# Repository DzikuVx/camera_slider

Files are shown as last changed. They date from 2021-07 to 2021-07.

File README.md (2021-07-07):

# DIY Motorized Camera Slider

Video presentation https://youtu.be/z8LCp77dOxo

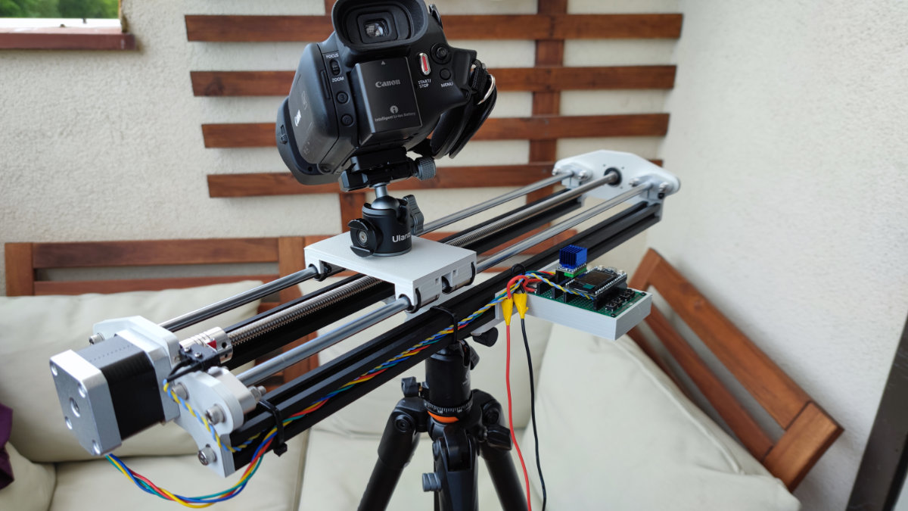
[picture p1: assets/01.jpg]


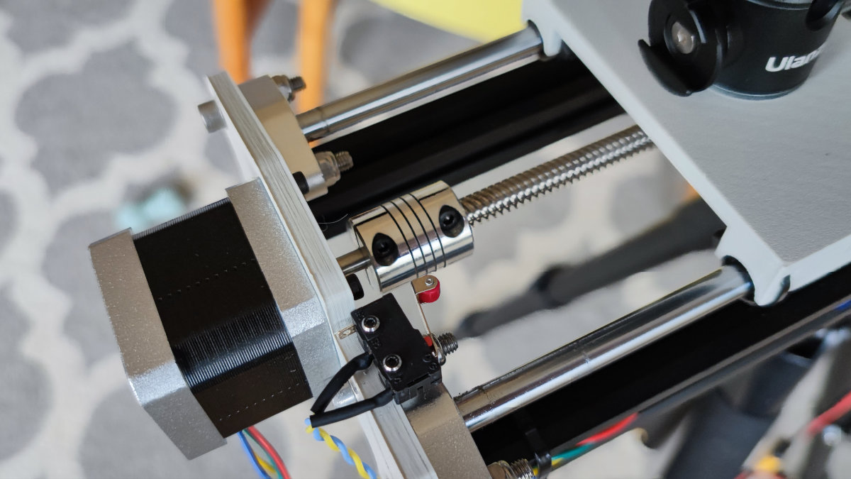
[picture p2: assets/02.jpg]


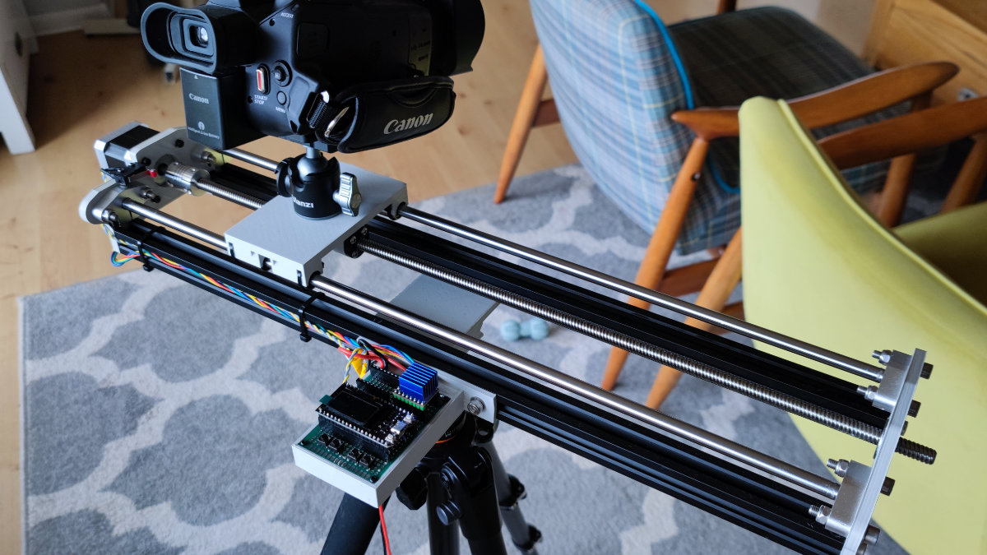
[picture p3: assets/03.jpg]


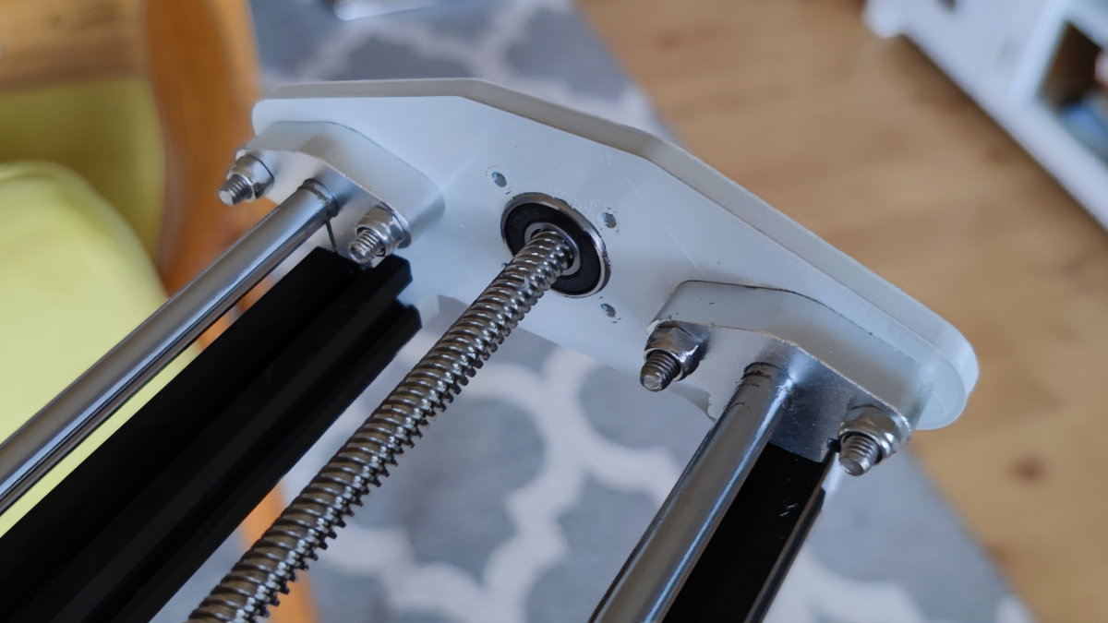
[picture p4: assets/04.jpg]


# ESP32 pinouts

| Function | ESP32 pin |
| --- | --- |
| TMC2209 direction pin | 13 |
| TMC2209 step pin | 12 |
| End-stop switch | 17 |
| TMC2209 Enable | 14 |
| Button #1 | 21 |
| Button #1 | 22 |
| Button #1 | 19 |
| Button #1 | 23 |

# User interface

Web Interface over WiFi is recommended. Connect to `DiyCameraSlider` WiFi with password `123456789` and use `http://192.168.4.1` URL.

Buttons are for emergency situations.

# Other

* TMC2209 should be configured in 8 microstep mode - MS1 and MS2 pulled to GND
* Tripod mount is compatible with Arca Swiss

#  Dependencies

* [AsyncTCP](https://github.com/me-no-dev/AsyncTCP)
* [ESPAsyncWebServer](https://github.com/me-no-dev/ESPAsyncWebServer)

# BOM

* [TTGO ESP32 with OLED](https://bit.ly/2G3qTSO)
* [TMC2209 stepper driver](https://bit.ly/3yxFSKa)
* [Tactile buttons](http://bit.ly/2Kzawy3)
* 60x90 universal PCB
* [TR8 8mm lead screw nut](https://bit.ly/3jS5PQQ)
* [NEMA17 stepper motor](https://bit.ly/3yv4bZh)
* [T8 8mm lead screw](https://bit.ly/3hDNhRs)
* [2x 500mm linear rod 8mm diameter](https://bit.ly/3eajnDF)
* [5x8mm coupler](https://bit.ly/3dMOrZR)
* [4x linear rod holder](https://bit.ly/3xndEBR)
* [4x LM8UU linear bearings](https://bit.ly/36hJqUK)
* 608 2RS 8x22x7mm bearing
* [Tripod head](https://bit.ly/3wtL7te)
* Tripod screw to attach the head
* 2x 500mm  2020 V-slot alu profiles
* 2020 hammer nuts
* M3 and M5 nuts and screws
* End switch
* 5V stepdown voltage regulator
* cables

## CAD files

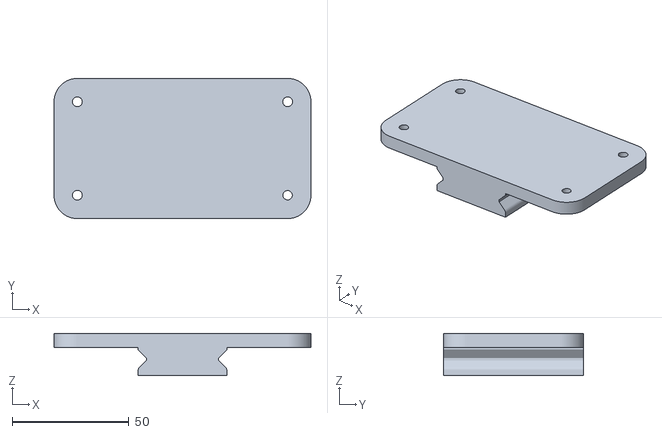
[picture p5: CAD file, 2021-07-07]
stl/tripod-mount.stl
110.0 x 60.0 x 18.0

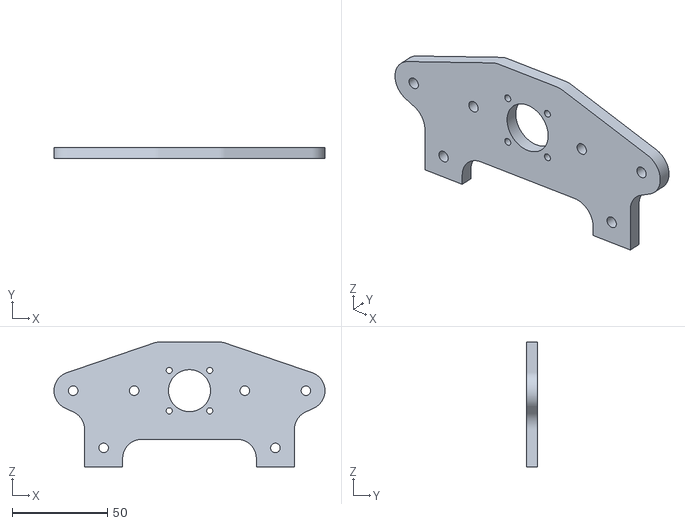
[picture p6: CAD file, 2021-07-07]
stl/end-plate-b.stl
142.0 x 6.00 x 65.5

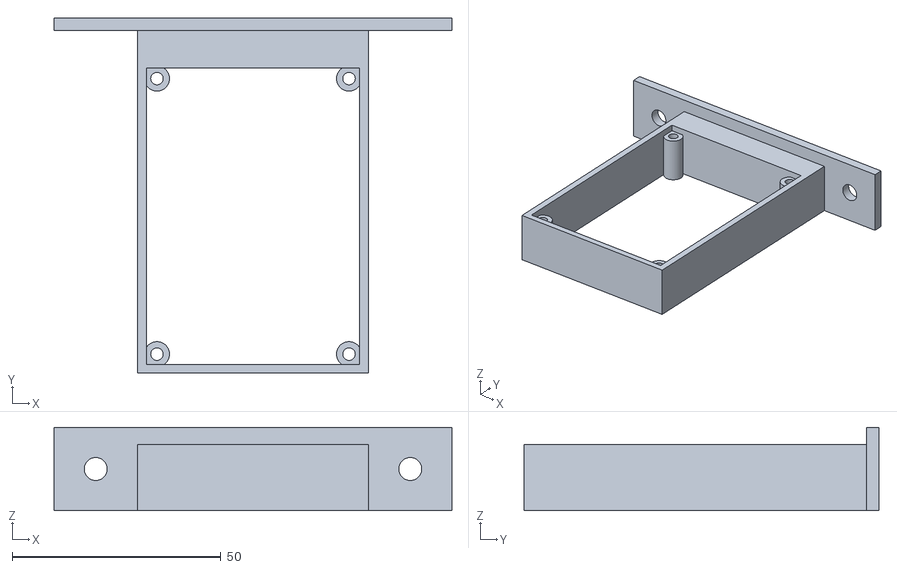
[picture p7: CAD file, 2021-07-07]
stl/pcb-holder.stl
95.3 x 85.0 x 20.0

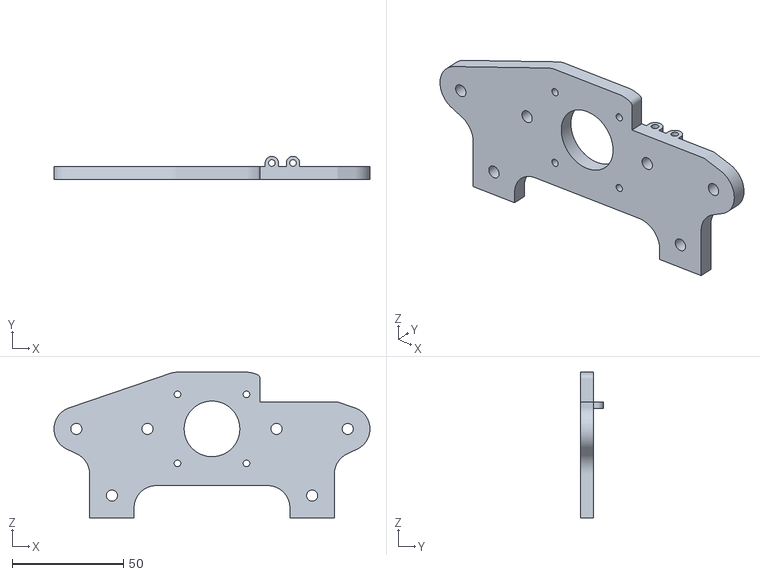
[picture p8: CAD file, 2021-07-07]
stl/end-plate-a.stl
142.0 x 10.5 x 65.5

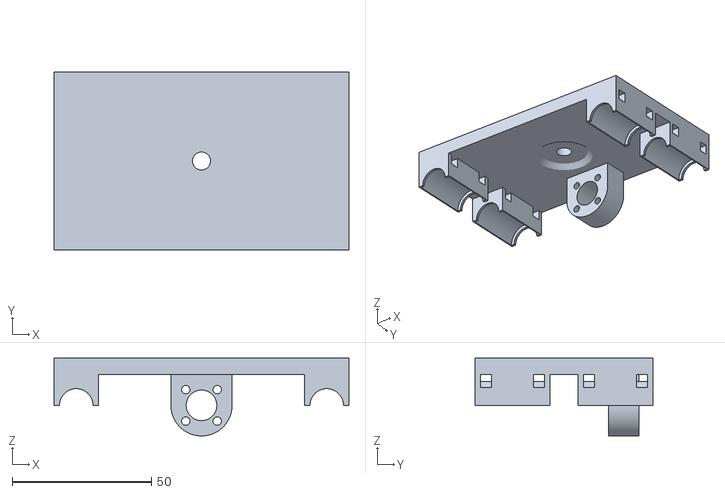
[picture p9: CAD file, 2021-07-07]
stl/platform.stl
106.0 x 64.0 x 28.0

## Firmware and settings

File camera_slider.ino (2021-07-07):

// #include <Wire.h>
#include "QmuTactile.h"
#include "filter.h"
#include <WiFi.h>
#include <AsyncTCP.h>
#include <ESPAsyncWebServer.h>

#define PID_UPDATE_TASK_MS 50

#define PIN_STEP1_DIRECTION 13
#define PIN_STEP1_STEP 12

#define PIN_STEP2_DIRECTION 18
#define PIN_STEP2_STEP 5

#define PIN_END_STOP 17

#define PIN_STEP_ENABLE 14

#define PIN_BUTTON_1 21
#define PIN_BUTTON_2 22
#define PIN_BUTTON_3 19
#define PIN_BUTTON_4 23

#define I2C1_SDA_PIN 4
#define I2C1_SCL_PIN 15

#define I2C2_SDA_PIN 27
#define I2C2_SCL_PIN 26

// TwoWire I2C1 = TwoWire(0); //OLED bus
// TwoWire I2C2 = TwoWire(1); //VL53L0X bus

QmuTactile button1(PIN_BUTTON_1);
QmuTactile button2(PIN_BUTTON_2);
QmuTactile button3(PIN_BUTTON_3);
QmuTactile button4(PIN_BUTTON_4);
QmuTactile buttonEnd(PIN_END_STOP);

// TaskHandle_t driverPid;


// QmuPid distanceToStep(0.1, 0, 50, 0);

// Adafruit_VL53L0X lox = Adafruit_VL53L0X();

enum systemFlags_e
{
  SYSTEM_FLAG_NONE = 0,                  //  0
  SYSTEM_FLAG_NEEDS_CALIBRATION = 1 << 0,  //  1
  SYSTEM_FLAG_CALIBRATING = 1 << 1,     //  2
  SYSTEM_FLAG_OPERATIONAL = 1 << 2, // 4 
  SYSTEM_FLAG_FORCE_FORWARD = 1 << 3, // 8 
  SYSTEM_FLAG_MOVE_TO_POSITION = 1 << 4, // 8 
  SYSTEM_FLAG_EMERGENCY_STOP = 1 << 5, // 8 
  SYSTEM_FLAG_REQUESTING_POSITION = 1 << 6, // 16
};

uint8_t _systemFlags;
pt1Filter_t targetPositionFilter;

volatile int stepsPerSecond[2] = {0};

#define SPEED_SLOW 750
#define SPEED_MID 1500
#define SPEED_FAST 3000

int32_t maxSpeed = SPEED_MID;

int32_t currentPosition[2] = {0};   
int32_t targetPosition[2] = {0};    //Hardware operated Position
int32_t requestedPosition[2] = {0}; //User requested Position

AsyncWebServer server(80);

const char* ssid = "DiyCameraSlider";
const char* password = "123456789";

void notFound(AsyncWebServerRequest *request) {
    request->send(404, "text/plain", "Not found");
}

String pageContent() {
    String pageContent;
    pageContent = "<!DOCTYPE html><html>";
    pageContent += "<head><meta name=\"viewport\" content=\"width=device-width, initial-scale=1\">";
    pageContent += "<link rel=\"icon\" href=\"data:,\">";
    pageContent += "<style>html { font-family: Helvetica; display: inline-block; margin: 0px auto; text-align: center;}";
    pageContent += ".button { background-color: #4CAF50; border: none; color: white; padding: 16px 40px; text-decoration: none; font-size: 30px; margin: 2px; cursor: pointer;}";
    pageContent += ".button-small { background-color: #0000ff; border: none; color: white; padding: 8px 20px; text-decoration: none; font-size: 15px; margin: 2px; cursor: pointer;}";
    pageContent += ".button2 {background-color: #ff0000;}</style></head>";
    
    pageContent += "<body><h1>DIY Camera Slider</h1>";
    
    pageContent += "<p><a href=\"/forward\"><button class=\"button\">Forward</button></a></p>";
    pageContent += "<p><a href=\"/stop\"><button class=\"button button2\">Stop</button></a></p>";
    pageContent += "<p><a href=\"/backward\"><button class=\"button\">Backward</button></a></p>";
    
    pageContent += "<p>";
    pageContent += "<a href=\"/slow\"><button class=\"button-small\">Slow</button></a>";
    pageContent += "<a href=\"/mid\"><button class=\"button-small\">Mid</button></a>";
    pageContent += "<a href=\"/fast\"><button class=\"button-small\">Fast</button></a>";
    pageContent += "</p>";

    pageContent += "</body></html>";

    return pageContent;
}

void setup()
{
    Serial.begin(115200);

    WiFi.softAP(ssid, password);
    IPAddress IP = WiFi.softAPIP();
    Serial.print("AP IP address: ");
    Serial.println(IP);

    server.on("/", HTTP_GET, [](AsyncWebServerRequest *request){
        request->send(200, "text/html", pageContent());
    });

    server.on("/forward", HTTP_GET, [](AsyncWebServerRequest *request){
        requestedPosition[0] = 81000;
        _systemFlags |= SYSTEM_FLAG_REQUESTING_POSITION;
        request->send(200, "text/html", pageContent());
    });

    server.on("/backward", HTTP_GET, [](AsyncWebServerRequest *request){
        requestedPosition[0] = 0;
        _systemFlags |= SYSTEM_FLAG_REQUESTING_POSITION;
        request->send(200, "text/html", pageContent());
    });

    server.on("/stop", HTTP_GET, [](AsyncWebServerRequest *request){
        requestedPosition[0] = currentPosition[0];
        targetPosition[0] = currentPosition[0];
        _systemFlags |= SYSTEM_FLAG_REQUESTING_POSITION;
        request->send(200, "text/html", pageContent());
    });

    server.on("/slow", HTTP_GET, [](AsyncWebServerRequest *request){
        maxSpeed = SPEED_SLOW;
        request->send(200, "text/html", pageContent());
    });

    server.on("/mid", HTTP_GET, [](AsyncWebServerRequest *request){
        maxSpeed = SPEED_MID;
        request->send(200, "text/html", pageContent());
    });

    server.on("/fast", HTTP_GET, [](AsyncWebServerRequest *request){
        maxSpeed = SPEED_FAST;
        request->send(200, "text/html", pageContent());
    });

    server.onNotFound(notFound);
    server.begin();

    // pinMode(16, OUTPUT);
    // digitalWrite(16, LOW); // set GPIO16 low to reset OLED
    // delay(50);
    // digitalWrite(16, HIGH); // while OLED is running, must set GPIO16 to high

    // I2C1.begin(I2C1_SDA_PIN, I2C1_SCL_PIN, 50000);
    // I2C2.begin(I2C2_SDA_PIN, I2C2_SCL_PIN, 400000);

    pinMode(PIN_STEP1_DIRECTION, OUTPUT);
    pinMode(PIN_STEP1_STEP, OUTPUT);
    pinMode(PIN_STEP_ENABLE, OUTPUT);

    digitalWrite(PIN_STEP1_DIRECTION, LOW);
    digitalWrite(PIN_STEP1_STEP, LOW);

    digitalWrite(PIN_STEP_ENABLE, LOW);

    button1.start();
    button2.start();
    button3.start();
    button4.start();
    buttonEnd.start();

    _systemFlags |= SYSTEM_FLAG_NEEDS_CALIBRATION;

    // xTaskCreatePinnedToCore(
    //     driverTaskHandler, /* Function to implement the task */
    //     "driverTask",              /* Name of the task */
    //     10000,                  /* Stack size in words */
    //     NULL,                   /* Task input parameter */
    //     0,                      /* Priority of the task */
    //     &driverTask,       /* Task handle. */
    //     0);

    // xTaskCreatePinnedToCore(
    //     pidTaskHandler, /* Function to implement the task */
    //     "driverPid",              /* Name of the task */
    //     10000,                  /* Stack size in words */
    //     NULL,                   /* Task input parameter */
    //     0,                      /* Priority of the task */
    //     &driverPid,       /* Task handle. */
    // 0);

}

uint32_t nextSlewRate = 0;

void loop()
{
	button1.loop();
	button2.loop();
	button3.loop();
	button4.loop();
    buttonEnd.loop();

    if (button1.getState() == TACTILE_STATE_SHORT_PRESS) {
        requestedPosition[0] = 1000;
        _systemFlags |= SYSTEM_FLAG_REQUESTING_POSITION;
    }

    if (button2.getState() == TACTILE_STATE_SHORT_PRESS) {
        requestedPosition[0] = 5000;
        _systemFlags |= SYSTEM_FLAG_REQUESTING_POSITION;
    }

    if (button3.getState() == TACTILE_STATE_SHORT_PRESS) {
        requestedPosition[0] = 0;
        _systemFlags |= SYSTEM_FLAG_REQUESTING_POSITION;
    }

    if (button4.getState() == TACTILE_STATE_SHORT_PRESS) {
        requestedPosition[0] = 81000;
        _systemFlags |= SYSTEM_FLAG_REQUESTING_POSITION;
    }

    // When requested position settled, settle down
    if ((_systemFlags & SYSTEM_FLAG_REQUESTING_POSITION) && targetPosition[0] == requestedPosition[0]) {
        _systemFlags &= ~SYSTEM_FLAG_REQUESTING_POSITION;
    }

    if (millis() > nextSlewRate) {
        if (_systemFlags & SYSTEM_FLAG_REQUESTING_POSITION) {

            int32_t error = requestedPosition[0] - targetPosition[0];
            int32_t acceleration = error * 100; // In steps per second
            //Constain acceleration
            acceleration = constrain(acceleration, -81000, 81000);
            targetPosition[0] = targetPosition[0] + (acceleration / 100);
        }

        nextSlewRate = millis() + 10;
    }

    if ((_systemFlags & SYSTEM_FLAG_NEEDS_CALIBRATION) && !buttonEnd.checkFlag(TACTILE_FLAG_PRESSED)) {
        stepsPerSecond[0] = 0;
        _systemFlags &= ~SYSTEM_FLAG_NEEDS_CALIBRATION;
        _systemFlags |= SYSTEM_FLAG_CALIBRATING;
    }

    if ((_systemFlags & SYSTEM_FLAG_NEEDS_CALIBRATION) && buttonEnd.checkFlag(TACTILE_FLAG_PRESSED)) {
        _systemFlags |= SYSTEM_FLAG_FORCE_FORWARD;
        stepsPerSecond[0] = 100;
    }

    if (_systemFlags & SYSTEM_FLAG_CALIBRATING) {
        if (!buttonEnd.checkFlag(TACTILE_FLAG_PRESSED)) {
            stepsPerSecond[0] = -5000;
        } else {
            stepsPerSecond[0] = 0;
            _systemFlags &= ~SYSTEM_FLAG_CALIBRATING;
            currentPosition[0] = -800;
            targetPosition[0] = 0;
            _systemFlags |= SYSTEM_FLAG_MOVE_TO_POSITION;
        }
    }

    if (_systemFlags & SYSTEM_FLAG_OPERATIONAL && buttonEnd.checkFlag(TACTILE_FLAG_PRESSED)) {
        _systemFlags |= SYSTEM_FLAG_EMERGENCY_STOP;
    }

#define MIN_SPEED 400
#define SPEED_CONTROLLER_P 8.0f

    /*
     * Position to speed
     */
    if (_systemFlags & SYSTEM_FLAG_MOVE_TO_POSITION) {

        targetPosition[0] = constrain(targetPosition[0], 0, 81000);

        int32_t error = targetPosition[0] - currentPosition[0];

        int32_t targetSpeed = error * SPEED_CONTROLLER_P;

        if (targetSpeed > maxSpeed) {
            targetSpeed = maxSpeed;
        } else if (targetSpeed < -maxSpeed) {
            targetSpeed = -maxSpeed;
        } else if (targetSpeed < maxSpeed && targetSpeed > 0) {
            targetSpeed = maxSpeed;
        } else if (targetSpeed > -maxSpeed && targetSpeed < 0) {
            targetSpeed = -maxSpeed;
        }
        
        if (error != 0) {
            stepsPerSecond[0] = targetSpeed;
        } else {
            _systemFlags |= SYSTEM_FLAG_OPERATIONAL;
            stepsPerSecond[0] = 0;
        }
    }

    static unsigned long nextChange = 0;
    static uint8_t currentState = LOW;

    if (_systemFlags & SYSTEM_FLAG_EMERGENCY_STOP) {
        digitalWrite(PIN_STEP1_DIRECTION, LOW);
        digitalWrite(PIN_STEP1_STEP, LOW);
    } else {
        
        if (stepsPerSecond[0] == 0) {
            currentState = LOW;
            digitalWrite(PIN_STEP1_STEP, LOW);
        } else {
            if (micros() > nextChange) {

                if (currentState == LOW) {
                    currentState = HIGH;
                    nextChange = micros() + 30;

                    if (stepsPerSecond[0] > 0) {
                        currentPosition[0]++;
                    } else if (stepsPerSecond[0] < 0) {
                        currentPosition[0]--;
                    }
                } else {
                    currentState = LOW;
                    nextChange = micros() + (1000 * abs(1000.0f / stepsPerSecond[0])) - 30;
                }

                if (stepsPerSecond[0] > 0) {
                    digitalWrite(PIN_STEP1_DIRECTION, LOW);
                } else {
                    digitalWrite(PIN_STEP1_DIRECTION, HIGH);
                }
                digitalWrite(PIN_STEP1_STEP, currentState);
            }
        }
    
    }
}
